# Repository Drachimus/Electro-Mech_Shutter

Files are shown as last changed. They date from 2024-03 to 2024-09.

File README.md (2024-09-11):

# Electro-Mechanical Shutter Controller
This is a controller intended to control solonoid operated electromechanical shutters typically used fro large format photography.
It uses a Raspberry PI Pico as the main control and can operate off batteries as included with the current files. (18650x4 in my case)
The power supply can be adpted to tool batteries or AC adapters as is apropriate for your shutter.
One limitation is my design is that the control is designed to operate with a MOSFET controlling up to 24 volts DC and will not work as is for an AC operated shutter as can be found in some packard shutters.

## Wiring and construction:
  
  This will be covered in detail in a Youtube video found here;
  YouTube link (https://youtu.be/-WX2WRZfZw8)
  
But assembly of the core system can also be accomplished by following the wiring diagram included in the code folder.

Wiring diagram

## Code:

  The code is written entirely in Python. To load the firmware to your Pico;
  - hold the boot button down on the pico while plugging it into your computer
  - when the Pico conects to your computer, it will show as a flash drive. Drag the circuit python UF2 downloaded from [Here](https://circuitpython.org/board/raspberry_pi_pico/) into that drive and it will reboot automatically
  - Once rebooted, hold the boot button again while unplugging and replugging the pico from the computer if it doesn't automatically come back up as a drive.
  - drag the file main.py and the folder modules onto the pico
  - reboot the pico by cycling power and you should be good to go.

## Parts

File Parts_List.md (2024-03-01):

# Parts List

These are the parts needed for this project with links where available;

- PI Pico (find local supplier Here)
- 0.91 inch 128x32 OLED with I2C interface (from Amazon, Waveshare or RobotShop)
- Rotary encoder (From RobotShop, Ebay or Amazon)
- Buck converter (Any adjustable buck converter able to accept input of 9 to 30 volts DC input and able to output 5 volts DC will work)
- MOSFET (from Amazon or commonly found in many arduino starter packs)
- 1N4004 Silicon diode (from DigiKey)
- Solonoid driven electro-mechanical shutter (can be found on ebay or local marketplaces)
- Wiring 18 AWG for power and 20-24 AWG for signaling
- 18650 battery terminals (from Amazon)
- Wire connectors (optional) (ones I used found here)
- Single pole double throw switch for power
- hot shoe adapter for flash sync on aplicable shutters (from Amazon)

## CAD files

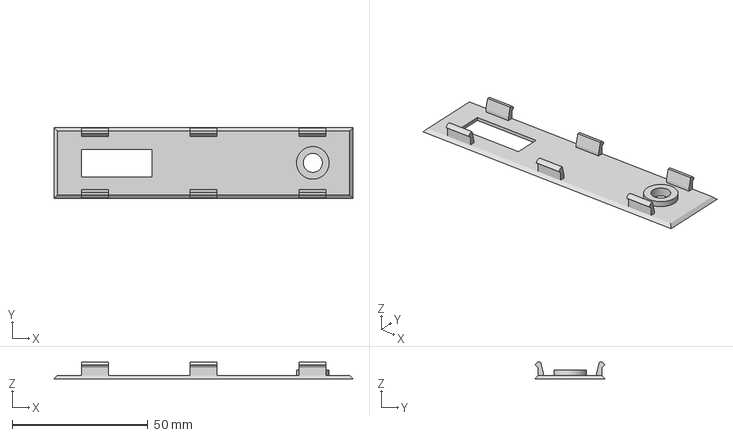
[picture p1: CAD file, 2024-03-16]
3D models/shutter control box top.3mf
110.0 x 26.0 x 6.20 mm

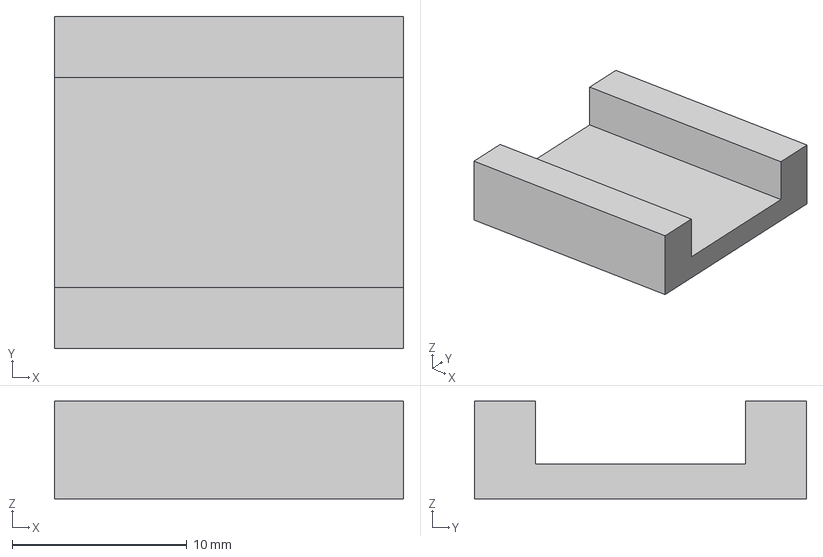
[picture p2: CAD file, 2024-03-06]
3D models/oled bracket.3mf
20.0 x 19.0 x 5.60 mm

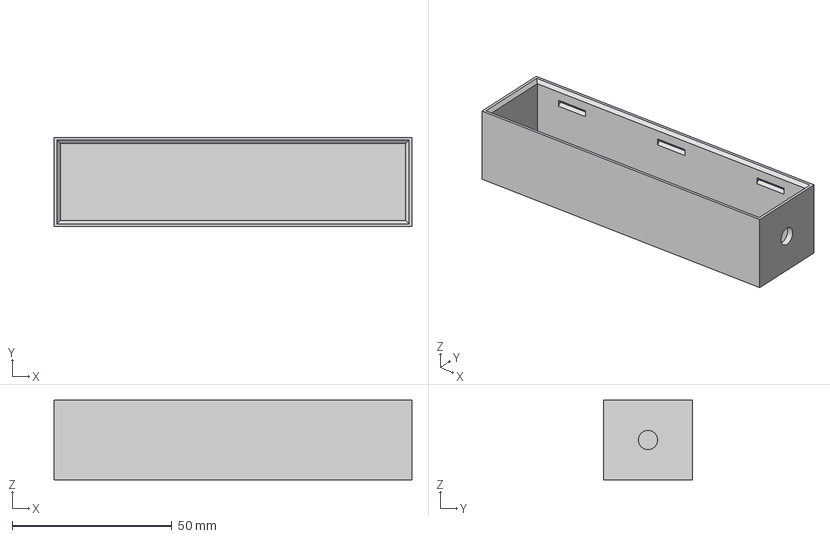
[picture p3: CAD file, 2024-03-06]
3D models/shutter control box.3mf
112.0 x 28.0 x 25.0 mm

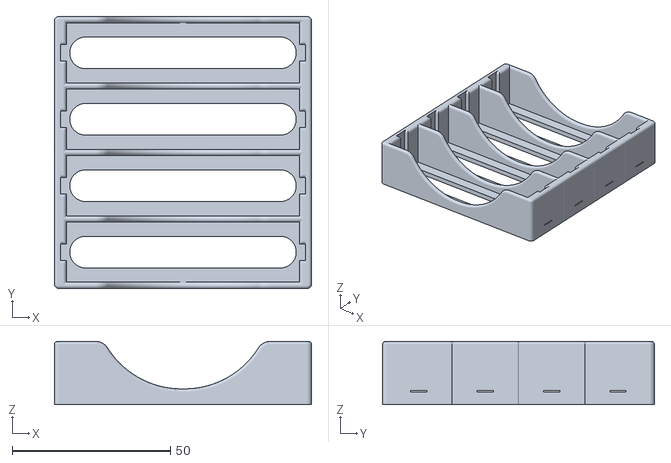
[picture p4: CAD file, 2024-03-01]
3D models/4_Battery.stl
81.4 x 86.0 x 20.0

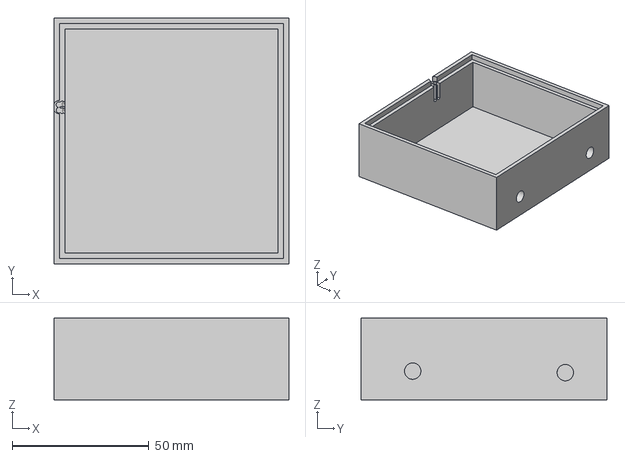
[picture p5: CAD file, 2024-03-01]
3D models/power box.3mf
86.0 x 90.0 x 30.0 mm

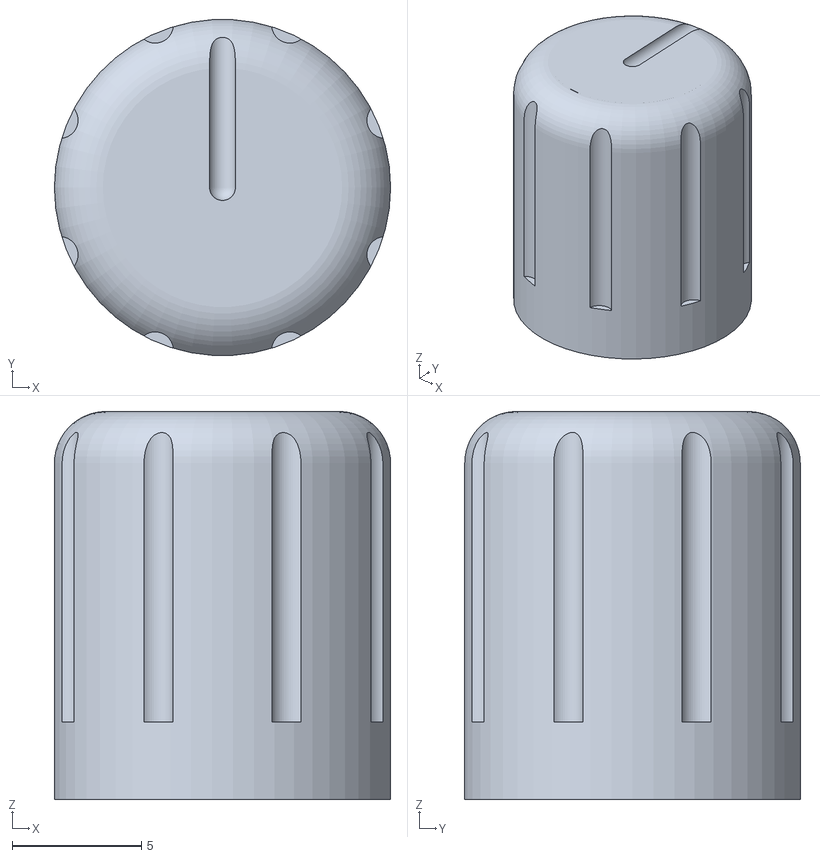
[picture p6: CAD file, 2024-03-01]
3D models/knob.stl
13.0 x 13.0 x 15.0

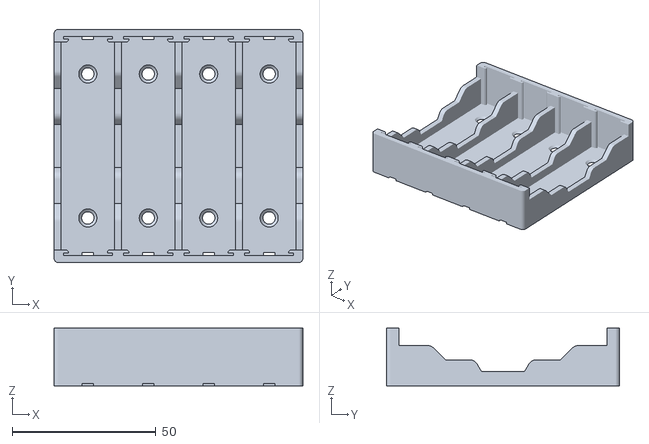
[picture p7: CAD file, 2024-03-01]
3D models/18650_holder-4.STL
86.5 x 81.0 x 20.0

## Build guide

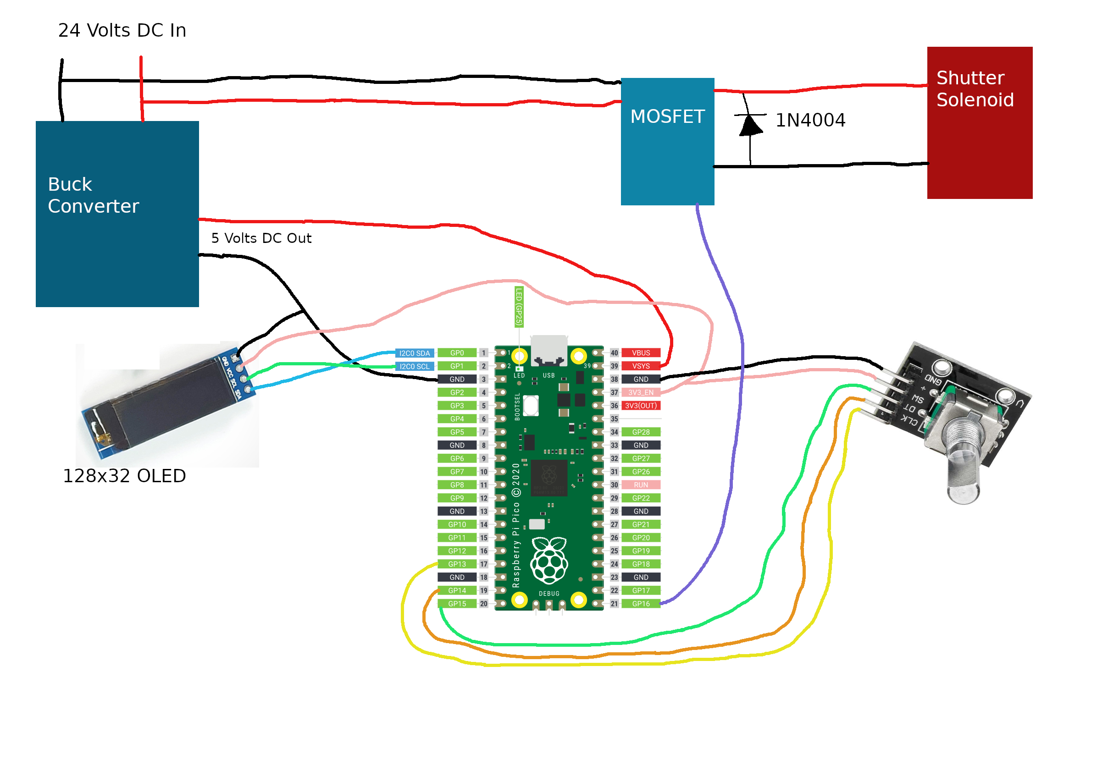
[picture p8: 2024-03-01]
Code/Wiring diagram.png

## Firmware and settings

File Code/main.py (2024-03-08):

# Shutter control for electro-mech shutter
# Authored by Drachimus



from rotary_irq_rp2 import RotaryIRQ
import time
from machine import Pin, I2C
from ssd1306 import SSD1306_I2C

i2c=I2C(0,sda=Pin(0), scl=Pin(1), freq=400000)
oled = SSD1306_I2C(128, 32, i2c)
SW=Pin(15,Pin.IN,Pin.PULL_UP)  # shutter fire button pulling to grnd when fired
ind_led = Pin(25, Pin.OUT)     # diagnostic indicator onboard led used pi pico
shut_relay = Pin(16, Pin.OUT)  # output pin conected to control relay for shutter
shut_relay.value(0)


#function to actuate the shutter mechanism

def shut_fire(shut_delay):
    
    if shut_delay == 1:
        if shut_relay.value()==1:
            shut_relay.value(0)
            ind_led.value(0)
            oled.init_display()
            oled.rotate(2)
            oled.text("Shutter", 0, 0, 32)
            oled.text("Closed", 0, 12, 32)
            oled.show()
            time.sleep(0.5)
            global update_display
            update_display = 1
        else:
            ind_led.value(1)
            shut_relay.value(1)
            oled.init_display()
            oled.rotate(2)
            oled.text("Shutter", 0, 0, 32)
            oled.invert(1)
            oled.text("OPEN", 16, 12, 32)
            oled.show()

        
    else:
        ind_led.value(1)
        shut_relay.value(1)
        time.sleep(shut_spd)
        shut_relay.value(0)
        ind_led.value(0)
        oled.text("Shutter Fired", 0, 24)
        oled.show()
        time.sleep(0.5)
        oled.init_display()
        update_display = 1



# setting displayed time for shutter and setting shutter open delay
# speeds going from 1/60 to 30 seconds plus focus

def scrn_txt(delay_sel):
    
    global shut_txt_val
    global shut_spd
    if delay_sel == 1:
        shut_txt_val="Focus"
    elif delay_sel == 2:
        shut_relay.value(0)
        shut_spd = 0.016
        shut_txt_val="1/60 Second"
    elif delay_sel == 3:
        shut_relay.value(0)
        shut_spd = 0.033
        shut_txt_val="1/30 Second"
    elif delay_sel == 4:
        shut_spd = 0.067
        shut_txt_val="1/15 Second"
    elif delay_sel == 5:
        shut_spd = 0.125
        shut_txt_val="1/8 Second"
    elif delay_sel == 6:
        shut_spd = 0.25
        shut_txt_val="1/4 Second"
    elif delay_sel == 7:
        shut_spd = 0.5
        shut_txt_val="1/2 Second"
    elif delay_sel == 8:
        shut_spd = 1
        shut_txt_val="1 Second"
    elif delay_sel == 9:
        shut_spd = 2
        shut_txt_val="2 Seconds"
    elif delay_sel == 10:
        shut_spd = 3
        shut_txt_val="3 Seconds"
    elif delay_sel == 11:
        shut_spd = 4
        shut_txt_val="4 Seconds"
    elif delay_sel == 12:
        shut_spd = 5
        shut_txt_val="5 Seconds"
    elif delay_sel == 13:
        shut_spd = 6
        shut_txt_val="6 Seconds"
    elif delay_sel == 14:
        shut_spd = 7
        shut_txt_val="7 Seconds"
    elif delay_sel == 15:
        shut_spd = 8
        shut_txt_val="8 Seconds"
    elif delay_sel == 16:
        shut_spd = 9
        shut_txt_val="9 Seconds"
    elif delay_sel == 17:
        shut_spd = 10
        shut_txt_val="10 Seconds"
    elif delay_sel == 18:
        shut_spd = 11
        shut_txt_val="11 Seconds"
    elif delay_sel == 19:
        shut_spd = 12
        shut_txt_val="12 Seconds"
    elif delay_sel == 20:
        shut_spd = 13
        shut_txt_val="13 Seconds"
    elif delay_sel == 21:
        shut_spd = 14
        shut_txt_val="14 Seconds"
    elif delay_sel == 22:
        shut_spd = 15
        shut_txt_val="15 Seconds"
    elif delay_sel == 23:
        shut_spd = 16
        shut_txt_val="16 Seconds"
    elif delay_sel == 24:
        shut_spd = 17
        shut_txt_val="17 Seconds"
    elif delay_sel == 25:
        shut_spd = 18
        shut_txt_val="18 Seconds"
    elif delay_sel == 26:
        shut_spd = 19
        shut_txt_val="19 Seconds"
    elif delay_sel == 27:
        shut_spd = 20
        shut_txt_val="20 Seconds"
    elif delay_sel == 28:
        shut_spd = 21
        shut_txt_val="21 Seconds"
    elif delay_sel == 29:
        shut_spd = 22
        shut_txt_val="22 Seconds"
    elif delay_sel == 30:
        shut_spd = 23
        shut_txt_val="23 Seconds"
    elif delay_sel == 31:
        shut_spd = 24
        shut_txt_val="24 Seconds"
    elif delay_sel == 32:
        shut_spd = 25
        shut_txt_val="25 Seconds"
    elif delay_sel == 33:
        shut_spd = 26
        shut_txt_val="26 Seconds"
    elif delay_sel == 34:
        shut_spd = 27
        shut_txt_val="27 Seconds"
    elif delay_sel == 35:
        shut_spd = 28
        shut_txt_val="28 Seconds"
    elif delay_sel == 36:
        shut_spd = 29
        shut_txt_val="29 Seconds"
    elif delay_sel == 37:
        shut_relay.value(0)
        shut_spd = 30
        shut_txt_val="30 Seconds"
    else:
        print("error")


# setting up rotary encoder input

r = RotaryIRQ(pin_num_clk=13,
              pin_num_dt=14,
              min_val=1,
              max_val=37,
              reverse=True,
              range_mode=RotaryIRQ.RANGE_WRAP)

val_old = r.value()
update_display = 1

while True:
    
    val_new = r.value()
    ind_led.value(0)

    if val_old != val_new: # acumulating rotary encoder steps
        
        val_old = val_new
        print('result =', val_new) #debug to terminal
        update_display = 1
        
    if SW.value()==0 and n==0:  # firing shutter when trigger button pressed center button on encoder used
        
        shut_fire(val_new)
        print("Button Pressed")  #debug to terminal
        n=1
        while SW.value()==0:  
           continue
    n=0  

    if update_display == 1:  # updating display with selected shutter speed and setting new speed value once new speed selected by turning rotary encoder
        
        update_display = 0
        scrn_txt(val_new)
        oled.init_display()
        oled.rotate(2)
        oled.text("Shutter Speed", 16, 0)
        oled.text(shut_txt_val, 8, 12)
        oled.show()

    time.sleep_ms(5)

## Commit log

2024-03-01 Create Wiring diagram.png
2024-03-03 Update shutter control box.3mf
    added opening for usb port
    [shutter control box.3mf]
2024-03-06 Updating Models
    Added clips to lid for control box
    [Shutter Control Box Lid.3mf, shutter control box top.3mf, shutter control box.3mf]
2024-03-06 Update oled bracket.3mf
    [oled bracket.3mf]
2024-03-16 updating control lid
    [Shutter Control Box Lid.3mf, shutter control box top.3mf]
